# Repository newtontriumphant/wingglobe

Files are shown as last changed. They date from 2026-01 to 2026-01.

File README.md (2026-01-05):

# WingGlobe

Quick Link Tree:

* [I. Introduction!](#i-introduction)
* [II. About This Project - Why I Chose To Make It!](#ii-about-this-project---why-i-chose-to-make-it)
* [III. About This Project - What Is It?!](#iii-about-this-project---what-is-it)
* [IV. Project Images And Technical Documentation!](#iv-project-images-and-technical-documentation)
* [V. Notes For Reviewers!](#v-notes-for-reviewers)
* [VI. Final Remarks!](#vi-final-remarks)
  
## I. Introduction!

Heyo! Thanks for reviewing my project! I'm **zsharpminor** (a.k.a. funkeudo), co-creator of FiddleStein, and this is WingGlobe, which is a (TL;DR) fully autonomous Weather-Telling Snow Globe with a custom propulsion mechanism, PWM control, backlighting, E-INK display, support for my existing ecosystem of temperature sensors, and a changeable theme. This project is being created with the support of Hack Club Blueprint, and it is an entry for Blueprint's 7-day Christmas-Themed Project Competition. I am aiming for this to be a **Tier 3** project (see section at the very end of this README for justification).



(Disclaimer: the above image is a **render**, this project is not actually built yet; CAD screenshots can be found in section IV).

**IMPORTANT REVIEWER'S NOTE:** there is a section at the **end** of this README.md file, please read through it before returning this project if possible :)

My BOM.csv is in the parent directory, additionally a link to my online BOM is https://docs.google.com/spreadsheets/d/1PTxZxDy7cq01-oPVpPEEbVuQKtVb_WSBa-1fNMrsmt8/. Thanks! :3

Before I get into why I made this project, I would like to extend a huge thanks to can can't aka kleigh (my hero), as well as sam, alex, zach, renran, deven, paolo, john cohn, olive, my teammates Max & Sidd, tanuki, nathan, everyone from AMD, and every single other equally important person that made Blueprint & Prototype happen - I literally found out about Blueprint (and Hack Club itself!) only a month and a week ago, finished a few projects and became a reviewer one week later, had the most fun I've _ever_ had at Prototype, as well as inspired myself to get back into hardware, and re-dedicate my life to electronics. I really appreciate everything each and every one of you has done, and, without further ado, here's why WingGlobe exists.

## II. About This Project - Why I Chose To Make It!

You're probably looking at this and asking me "why the hell would you make a smart snow globe?!" The answer is a bit more complex than you think!

To start off with, I'm going to say quite bluntly that this project wouldn't exist without the Blueprint Christmas Competition. Even though I've worked with hardware for years, got HM with a self playing violin, and have been a Blueprint reviewer for over a month, I **don't actually own a 3D printer** (I've been using my local library's for all of my past projects so far)! I was planning on buying one a few weeks ago, then I set myself the challenge of getting one through Blueprint by reviewing a lot and getting tickets - but my current pace is rather lackluster. In addition, I needed ideas for projects to build - Blueprint is awesome because you can ship literally anything you can imagine, as long as it's under a certain dollar amount; but I was facing a bit of a creative block until this competition came about! My first project idea was to make a laser projecting 2026 New Year's countdown - but then I remembered that New Years would be over by the time this project would be built! My goal with WingGlobe was to make a project that, while Christmas-themed, **doesn't rely on Christmas to exist** and can be used **at any time of the year**! (Christmas in July, anyone?)

Additionally, I've made an ecosystem of projects (including one that I made through Blueprint - my SmartBell!) that feature temperature and humidity sensors. I wanted them to seamlessly work together wirelessly somehow, and needed a way to make that possible. That is also the main reason I chose the ESP32-S3 for this project, besides the fact that I already owned one, that it would cut PCBA cost in half, and that it would require one less parcel to be shipped.

Finally, I've been interested in weather and meteorology in general for a few years now, and I always wanted a weather station that relied on multiple sources of data that I myself provide, in addition to the commercial weather reports available.

The Snow Globe that builds this project's core features an empty space for _any_ 3d model or figurine (assuming it's heavy enough to withstand the fan blowing snow around it!) - and I've chosen a Christmas-themed one for my first few months with WingGlobe to fit the competition's theme.

Finally, if you're wondering why it's called WingGlobe, it's a reference to aviation, where meteorology is key (bad name, I know, but it stuck!)

I wanted WingGlobe to fit these criteria:

* It **must** be overwhelmingly Christmas-themed.
* It **must** have a decent amount of hardware complexity.
* It **must** be usable outside of just Christmas season.
* It **must** predominantly integrate CAD and software instead of being _just_ hardware.
* It **must** be actually useful in everyday life.
* The PCB **must** be under 100x100mm, eligible for GSDL, and Economic PCBA.
* All parts of the project **must** be printable on the Bambu A1 Mini with minimal supports and t*nkering.

I think I did a pretty good job fitting these criteria, if I do say so myself. Anyways, enough yapping, here's what the project actually _does_:

## III. About This Project - What Is It?!

WingGlobe is basically a glorified weather report station powered by a SEEED Studios XIAO ESP-32-S3 (that I already own - more on that in Section V) that runs 16 addressable SK6812-MINI LEDs, as well as an onboard temp/humi/pressure sensor and a MOSFET powering a 4010 fan with PWM control. When the weather shifts, the snow globe is updated to match - calm weather is a white / light-blue gradient and no fan power, sunny weather is a yellow / light red gradient, sunrise and sunset are adapted to red / orange gradients, and during the night, the snow globe will be engulfed in a replica of the aurora borealis (clear sky) or simply white / dark blue (cloudy sky). The real fun begins when it rains! When the winds start, the 4010 fan's PWM controller starts to rev it up - the more dangerous the wind, the more the little snow in the globe will swirl around! I am planning to use lightweight cotton / styrofoam blend beads to imitate snow (my original idea of 3D printing them sadly failed), as well as a custom mesh that stops them from breaking the fan or going out of the top of the globe. WingGlobe's E-Ink can be customized with a touch pad on WingGlobe's PCB to show varying levels of information from varying sensors. Additionally, the fan and LEDs can be turned off with a switch on WingGlobe's side when not needed (i.e. overnight).

WingGlobe seamlessly integrates with my SmartBell, moonboard, ADS-B stations, and BarnSense projects to provide up to three different simultaneous readings of temperature, humidity, and pressure. WingGlobe also has a built-in sensor for indoor temperature and humidity (should be quite useful next to my soon-to-be 3D Printer!) For now, WingGlobe relies on commercially available data for wind readings, but I hope to create another project soon so that everything can be run off the grid and without requiring any API.

WingGlobe's ESP32-S3 connects via ESP-NOW and WiFi to fetch data from my close and far stations, respectively. You're halfway there, have a cookie! 🍪

## IV. Project Images And Technical Documentation!

### SCHEMATIC:

Screenshot 2026-01-01 at 3 03 01 PM

### PCB:

Screenshot 2026-01-01 at 3 03 26 PM

Screenshot 2026-01-01 at 3 04 12 PM

Screenshot 2026-01-01 at 3 04 40 PM

### CAD:

Screenshot 2026-01-01 at 3 05 12 PM

(base, with cutouts for PCB, fan, and globe)

Screenshot 2026-01-01 at 3 05 39 PM

(top, made to be glued onto base)

### CAD WITH PCB:

Screenshot 2026-01-01 at 3 06 51 PM

(top view)

Screenshot 2026-01-01 at 3 07 16 PM

(side view)

Screenshot 2026-01-01 at 3 07 37 PM

(bottom view)

Screenshot 2026-01-01 at 3 08 41 PM

(top - birds-eye view without lid)

### ASSEMBLED PRODUCT:

Screenshot 2026-01-01 at 3 09 26 PM

(Front - Angle One)

Screenshot 2026-01-01 at 3 09 43 PM

(Front - Angle Two)

Screenshot 2026-01-01 at 3 10 05 PM

(Top)

Screenshot 2026-01-01 at 3 10 19 PM

(Side)

Screenshot 2026-01-01 at 3 10 37 PM

(Bottom)

### CARTS:

Screenshot 2026-01-04 at 6 10 24 PM

(AliExpress Checkout)

Screenshot 2026-01-01 at 3 34 09 PM

(JLCPCB PCB Options)

Screenshot 2026-01-01 at 3 33 00 PM

(JLCPCB PCBA 1)

Screenshot 2026-01-01 at 3 33 20 PM

(JLCPCB PCBA 2)

Screenshot 2026-01-01 at 3 33 39 PM

(JLCPCB PCBA 3)

Screenshot 2026-01-01 at 3 34 48 PM

(JLCPCB Pre-Discounts)

Screenshot 2026-01-04 at 6 09 27 PM

(JLCPCB Final Checkout As Shown On BOM)

**NOTE**: My name was redacted using the Inspect Element tool as this repository is publically visible. If an unredacted screenshot is required, please DM me or return my project.

### I will self-fund the E-INK display due to the project tier being bumped down to T4.

### RENDER:



(My friend with Blender skills did this and it turned out amazing, so I'm making this my cover image!)

## V. Notes For Reviewers!

### Usage Of Pre-Built Devboard:

I chose to use the XIAO ESP32-S3 over making a custom ESP32 or RP2040 devboard base for three reasons:

1. I already own quite a few ESP32-S3s, making an ESP32 from scratch would more than **double** the PCBA cost at JLC, and make my order **ineligible** for GSDL shipping, which would push my budget to Tier 2.
2. I've already made a devboard, I know the hassles that are involved in wiring and routing, and I did not want to miss a single decoupling capacitor and risk my board being browned out.
3. I wanted to spend more time polishing software and CAD, and using a pre-built devboard gave me that opportunity.

Again, if this cannot be approved for Tier 3 due to a lack of complexity, I understand, and will remove parts to bring the budget down to a Tier 4.

### Why Are You Requesting Six Snow Globes?

Because it's the cheapest option available for a half-decent snowglobe on AliExpress. The next-cheapest was $7 for two, and I preferred to get six for $6.88.

All of my costs are optimized as **much as possible**, I'm using AliExpress for my items, and I've done my best to keep it in budget.

### Why Are You Requesting $10 More Than You Need For JLCPCB?

JLCPCB has a $10 coupon for PCBA (scroll up to the images section for proof). Said coupon expires in 2 days, and, knowing HCB, it will take more than 2 days to process this grant. If another coupon appears, I will return the difference immediately.

### "ThIs ReADmE iS AI gEnEraTEd!"

No, no it's not. I know how to use markdown, and I'll even occasionally use an em-dash—like so. That doesn't necessarily mean my README is automatically AI. Zero AI was used in the making of this project, and writing this text-heavy README alone took me two hours. If you need proof, I can provide a screen recording!

That's all, thanks! :D

## VI. Final Remarks!

Please ping or DM me on Slack (@zsharpminor) if you have any questions regarding my project.

Thank you so much for taking your precious time to read all the way through this extremely long README (I wanted to be well documented, okay?!)

You get a massive slice of vanilla cheesecake! :D 🍰

P.S. Happy New Year!!! I worked on this project literally as the clock struck 12 - I have a journal entry to prove it :)

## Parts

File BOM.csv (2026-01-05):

WingGlobe BOM
AliExpress Item | Link | Description | Price | Quantity | Running Total
1 | https://www.aliexpress.us/item/3256805177029030.html | (WHITE, 2-3.5mm 13g); used as snow | $2.08 | 1x 13g | $2.08
2 | https://www.aliexpress.us/item/3256806072050927.html | (SS12D06G5 10PCS); used for on/off | $1.76 | 1x 10 | $3.84
4 | https://www.aliexpress.us/item/3256807169365804.html | (6PCS with AL lid); snow globe housing | $6.88 | 1x 6 | $10.72
5 | https://www.aliexpress.us/item/3256806120222119.html | (5V, 4010); fan to power snow | $2.06 | 1x 1 | $12.69
AliExpress Total: | $12.69
JLCPCB Item
PCB | N/A | What makes WingGlobe work! | $2.00 | 1x 5 | $2.00
PCBA | N/A | Pay those poor Chinese laborers! | $25.63 | 1x 2 | $27.63
Shipping | N/A | This is GSDL - check screenshot for proof. | $14.63 | 1x 1 | $42.26
Taxes | N/A | I wish I was tax-exempt... | $1.79 | 1x 1 | $44.05
Payment Fee | N/A | What is this for, anyways?! | $0.50 | 1x 1 | $44.55
Discount | N/A | Hooray! | -$9.00 | 1x 1 | $35.55
JLCPCB Total: | $35.55
GRAND TOTAL: | $48.24
ROUNDED TOTAL: | $50
Notes: | My detailed JLCPCB BOM for PCBA and proof of GSDL are in cart screenshots.
 | If required, the detailed PCBA breakdown can be individually listed. Please DM me.

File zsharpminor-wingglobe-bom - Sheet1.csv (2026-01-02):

WingGlobe BOM
AliExpress Item | Link | Description | Price | Quantity | Running Total
1 | https://www.aliexpress.us/item/3256805177029030.html | (WHITE, 2-3.5mm 13g); used as snow | $2.08 | 1x 13g | $2.08
2 | https://www.aliexpress.us/item/3256806072050927.html | (SS12D06G5 10PCS); used for on/off | $1.76 | 1x 10 | $3.84
3 | https://www.aliexpress.us/item/3256805040417601.html | (SINK0290B2-BRW); used as display | $9.99 | 1x 1 | $13.83
4 | https://www.aliexpress.us/item/3256807169365804.html | (6PCS with AL lid); snow globe housing | $6.88 | 1x 6 | $20.71
5 | https://www.aliexpress.us/item/3256806120222119.html | (5V, 4010); fan to power snow | $2.06 | 1x 1 | $22.77
Shipping |  | Cheapest Possible | $8.97 | 1x 1 | $31.74
Taxes |  | I don't do tax evasion ;w; | $1.86 | 1x 1 | $33.60
Estimated Coupon |  | I hope this'll still be there! | -$0.20 | 1x 1 | $33.40
AliExpress Total: | $33.40
JLCPCB Item
PCB | N/A | What makes WingGlobe work! | $2.00 | 1x 5 | $2.00
PCBA | N/A | Pay those poor Chinese laborers! | $25.63 | 1x 2 | $27.63
Shipping | N/A | This is GSDL - check screenshot for proof. | $14.63 | 1x 1 | $42.26
Taxes | N/A | I wish I was tax-exempt... | $2.62 | 1x 1 | $44.88
Payment Fee | N/A | What is this for, anyways?! | $0.50 | 1x 1 | $45.38
JLCPCB Total: | $45.38
GRAND TOTAL: | $78.78
ROUNDED TOTAL: | $80
Notes: | My detailed JLCPCB BOM for PCBA and proof of GSDL are in cart screenshots.
 | If required, the detailed PCBA breakdown can be individually listed. Please DM me.
 | JLCPCB has a $10 coupon BUT it expires on January 3rd, which is why it's not
 | accounted for in this BOM. If another coupon becomes available, I will return the
 | extra $10.

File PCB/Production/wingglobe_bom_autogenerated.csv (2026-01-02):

Designator | Footprint | Quantity | Value | LCSC Part #
C1 | 0402 | 1 | 10 uF
C2 | 0402 | 1 | 0.1uF
D1, D10, D11, D12, D13, D14, D15, D16, D2, D3, D4, D5, D6, D7, D8, D9 | LED_SK6812MINI_PLCC4_3.5x3.5mm_P1.75mm | 16 | SK6812MINI
J1 | JST_XH_B2B-XH-A_1x02_P2.50mm_Vertical | 1 | Conn_01x02
J2 | PinHeader_1x08_P2.54mm_Vertical | 1 | Conn_01x08
Q1 | SOT-23 | 1 | AO3400A
R1 | 0402 | 1 | 330
R2 | 0402 | 1 | 10k
R3, R4 | 0402 | 2 | 4.7k
SW1 | SW_Slide_SPDT_Angled_CK_OS102011MA1Q | 1 | SW_SPDT
TP1 | TestPoint_Pad_D4.0mm | 1 | TOUCH
U1 | XIAO-ESP32S3-DIP | 1 | XIAO-ESP32-S3-DIP
U2 | Texas_PWSON-N6 | 1 | HDC1080

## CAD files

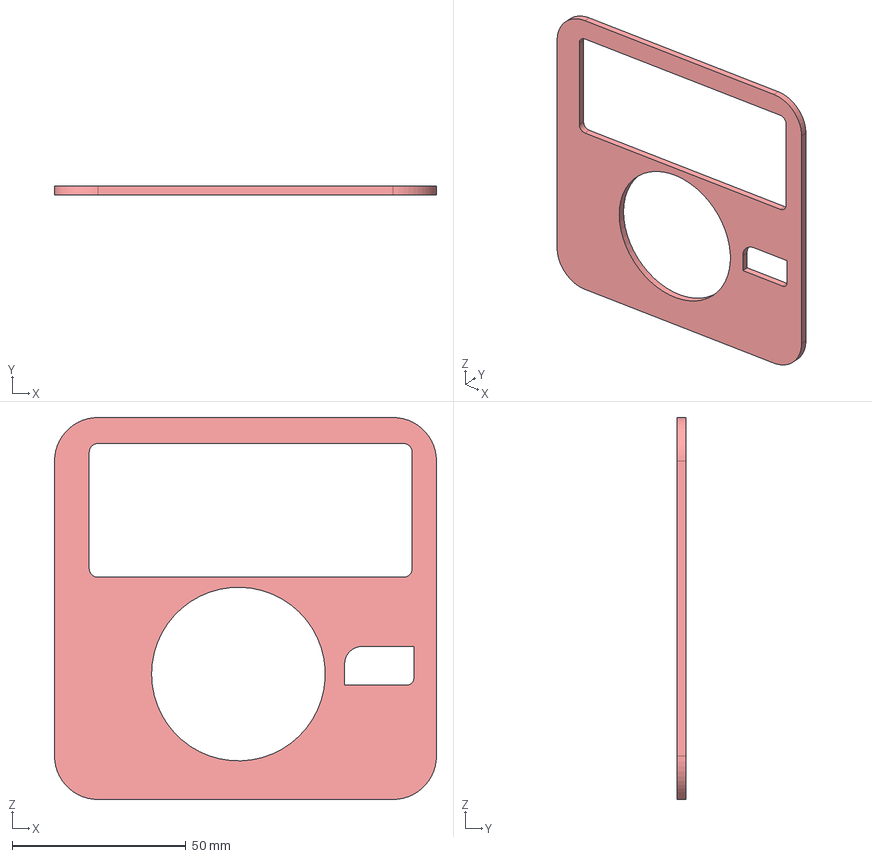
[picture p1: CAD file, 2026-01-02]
CAD/Housing/wingglobe_top.step
110.0 x 2.50 x 110.0 mm

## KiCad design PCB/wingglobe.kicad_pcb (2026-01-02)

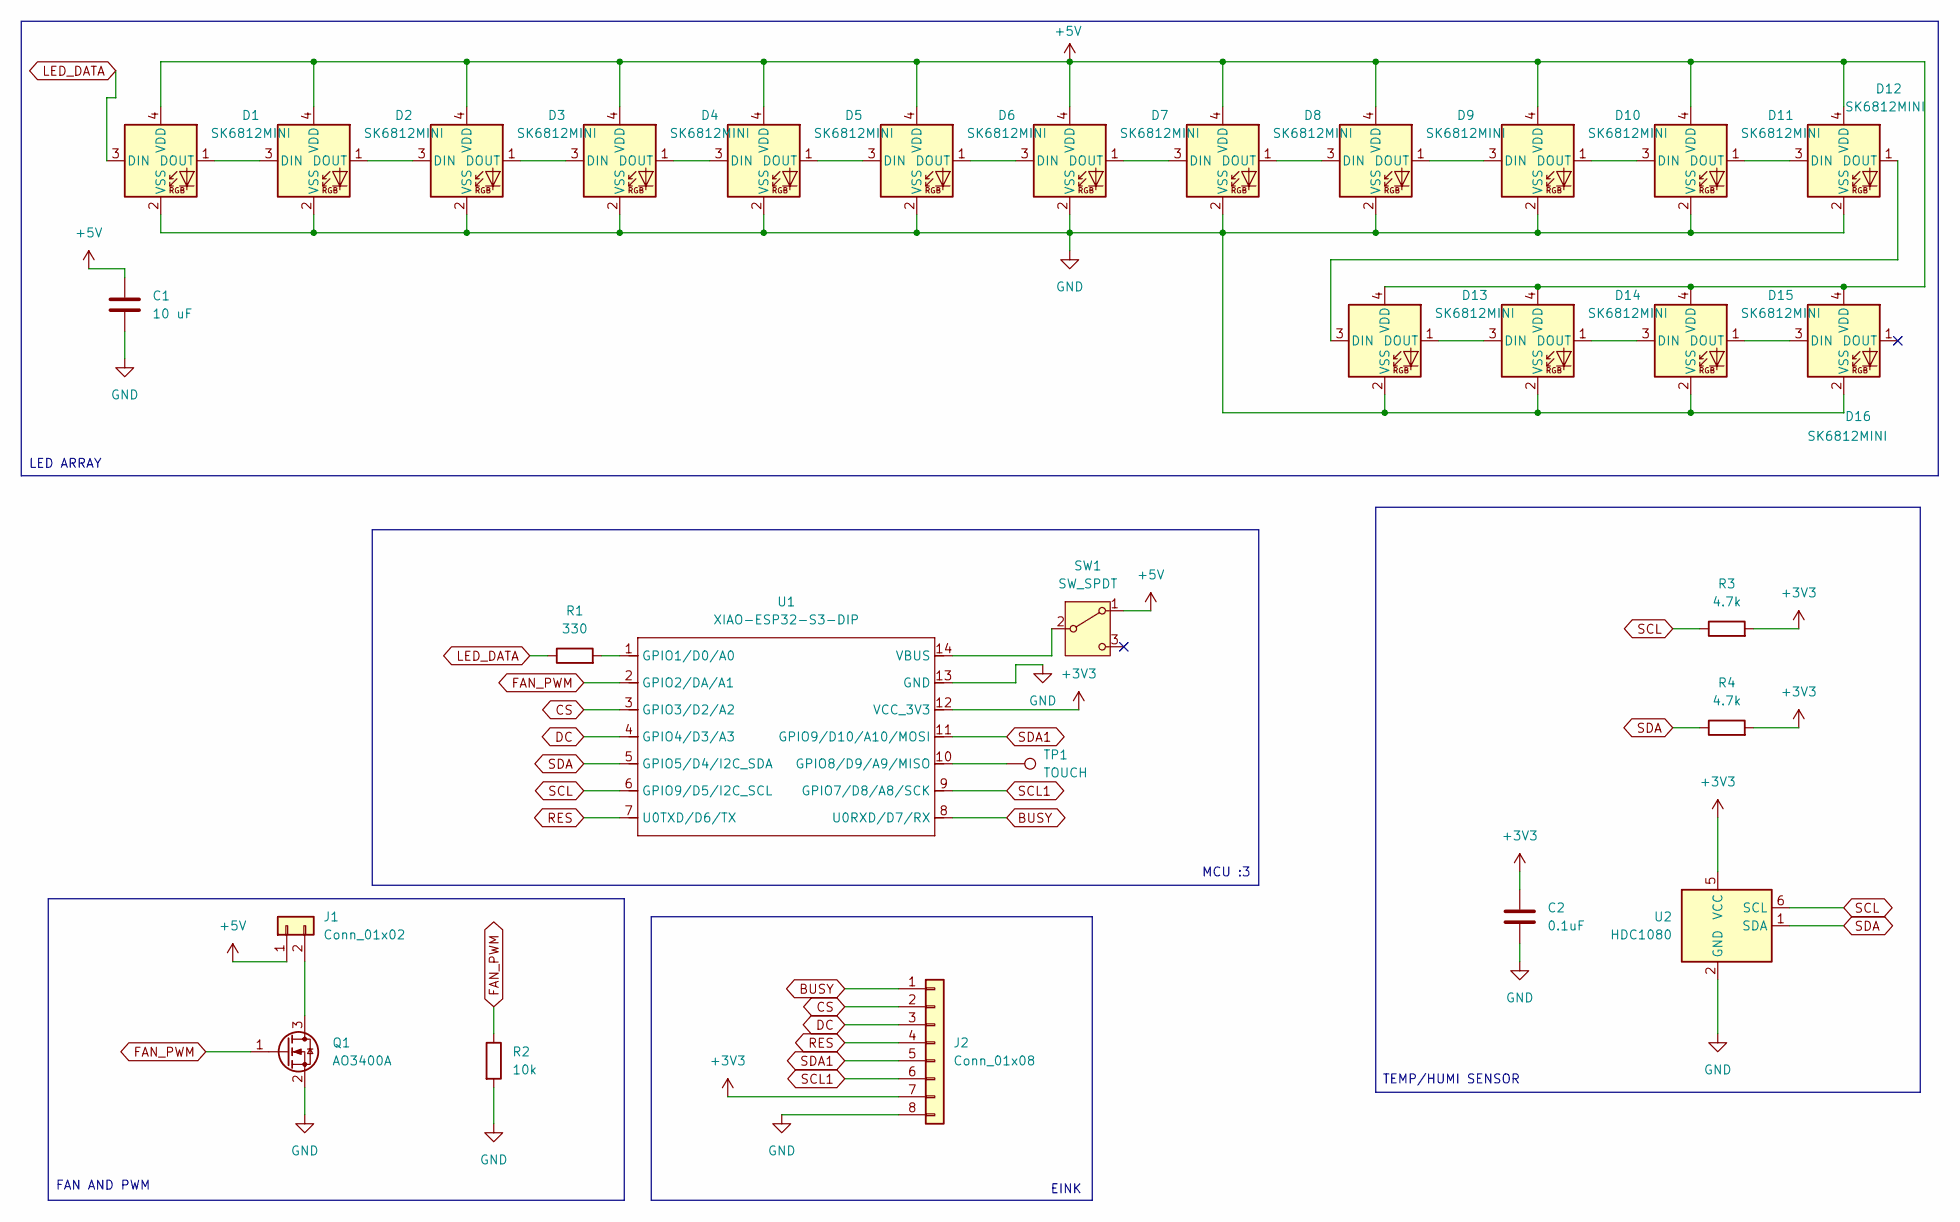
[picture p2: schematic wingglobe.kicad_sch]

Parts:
C1: 10 uF; C_0402_1005Metric
C2: 0.1uF; C_0402_1005Metric
D1, D2, D3, D4, D5, D6, D7, D8, D9, D10, D11, D12, D13, D14, D15, D16: SK6812MINI; LED_SK6812MINI_PLCC4_3.5x3.5mm_P1.75mm
J1: Conn_01x02; JST_XH_B2B-XH-A_1x02_P2.50mm_Vertical
J2: Conn_01x08; PinHeader_1x08_P2.54mm_Vertical
Q1: AO3400A; SOT-23
R1: 330; R_0402_1005Metric
R2: 10k; R_0402_1005Metric
R3, R4: 4.7k; R_0402_1005Metric
SW1: SW_SPDT; SW_Slide_SPDT_Angled_CK_OS102011MA1Q
TP1: TOUCH; TestPoint_Pad_D4.0mm
U1: XIAO-ESP32-S3-DIP; XIAO-ESP32S3-DIP
U2: HDC1080; Texas_PWSON-N6

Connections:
+3V3: C2.1, J2.7, R3.2, R4.2, U1.12 (VCC_3V3), U2.5 (VCC)
+5V: C1.1, D1.4 (VDD), D2.4 (VDD), D3.4 (VDD), D4.4 (VDD), D5.4 (VDD), D6.4 (VDD), D7.4 (VDD), D8.4 (VDD), D9.4 (VDD), D10.4 (VDD), D11.4 (VDD), D12.4 (VDD), D13.4 (VDD), D14.4 (VDD), D15.4 (VDD), D16.4 (VDD), J1.1, SW1.1 (A)
BUSY: J2.1, U1.8 (U0RXD/D7/RX)
CS: J2.2, U1.3 (GPIO3/D2/A2)
DC: J2.3, U1.4 (GPIO4/D3/A3)
FAN_PWM: Q1.1 (G), R2.1, U1.2 (GPIO2/DA/A1)
GND: C1.2, C2.2, D1.2 (VSS), D2.2 (VSS), D3.2 (VSS), D4.2 (VSS), D5.2 (VSS), D6.2 (VSS), D7.2 (VSS), D8.2 (VSS), D9.2 (VSS), D10.2 (VSS), D11.2 (VSS), D12.2 (VSS), D13.2 (VSS), D14.2 (VSS), D15.2 (VSS), D16.2 (VSS), J2.8, Q1.2 (S), R2.2, U1.13 (GND), U2.2 (GND)
LED_DATA: D1.3 (DIN), R1.1
unnamed: D1.1 (DOUT), D2.3 (DIN)
unnamed: D2.1 (DOUT), D3.3 (DIN)
unnamed: D3.1 (DOUT), D4.3 (DIN)
unnamed: D4.1 (DOUT), D5.3 (DIN)
unnamed: D5.1 (DOUT), D6.3 (DIN)
unnamed: D6.1 (DOUT), D7.3 (DIN)
unnamed: D7.1 (DOUT), D8.3 (DIN)
unnamed: D8.1 (DOUT), D9.3 (DIN)
unnamed: D9.1 (DOUT), D10.3 (DIN)
unnamed: D10.1 (DOUT), D11.3 (DIN)
unnamed: D11.1 (DOUT), D12.3 (DIN)
unnamed: D12.1 (DOUT), D13.3 (DIN)
unnamed: D13.1 (DOUT), D14.3 (DIN)
unnamed: D14.1 (DOUT), D15.3 (DIN)
unnamed: D15.1 (DOUT), D16.3 (DIN)
unnamed: J1.2, Q1.3 (D)
unnamed: SW1.2 (B), U1.14 (VBUS)
unnamed: R1.2, U1.1 (GPIO1/D0/A0)
unnamed: TP1.1, U1.10 (GPIO8/D9/A9/MISO)
RES: J2.4, U1.7 (U0TXD/D6/TX)
SCL: R3.1, U1.6 (GPIO9/D5/I2C_SCL), U2.6 (SCL)
SCL1: J2.6, U1.9 (GPIO7/D8/A8/SCK)
SDA: R4.1, U1.5 (GPIO5/D4/I2C_SDA), U2.1 (SDA)
SDA1: J2.5, U1.11 (GPIO9/D10/A10/MOSI)

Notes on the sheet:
TEMP/HUMI SENSOR
FAN AND PWM
EINK
MCU :3
LED ARRAY

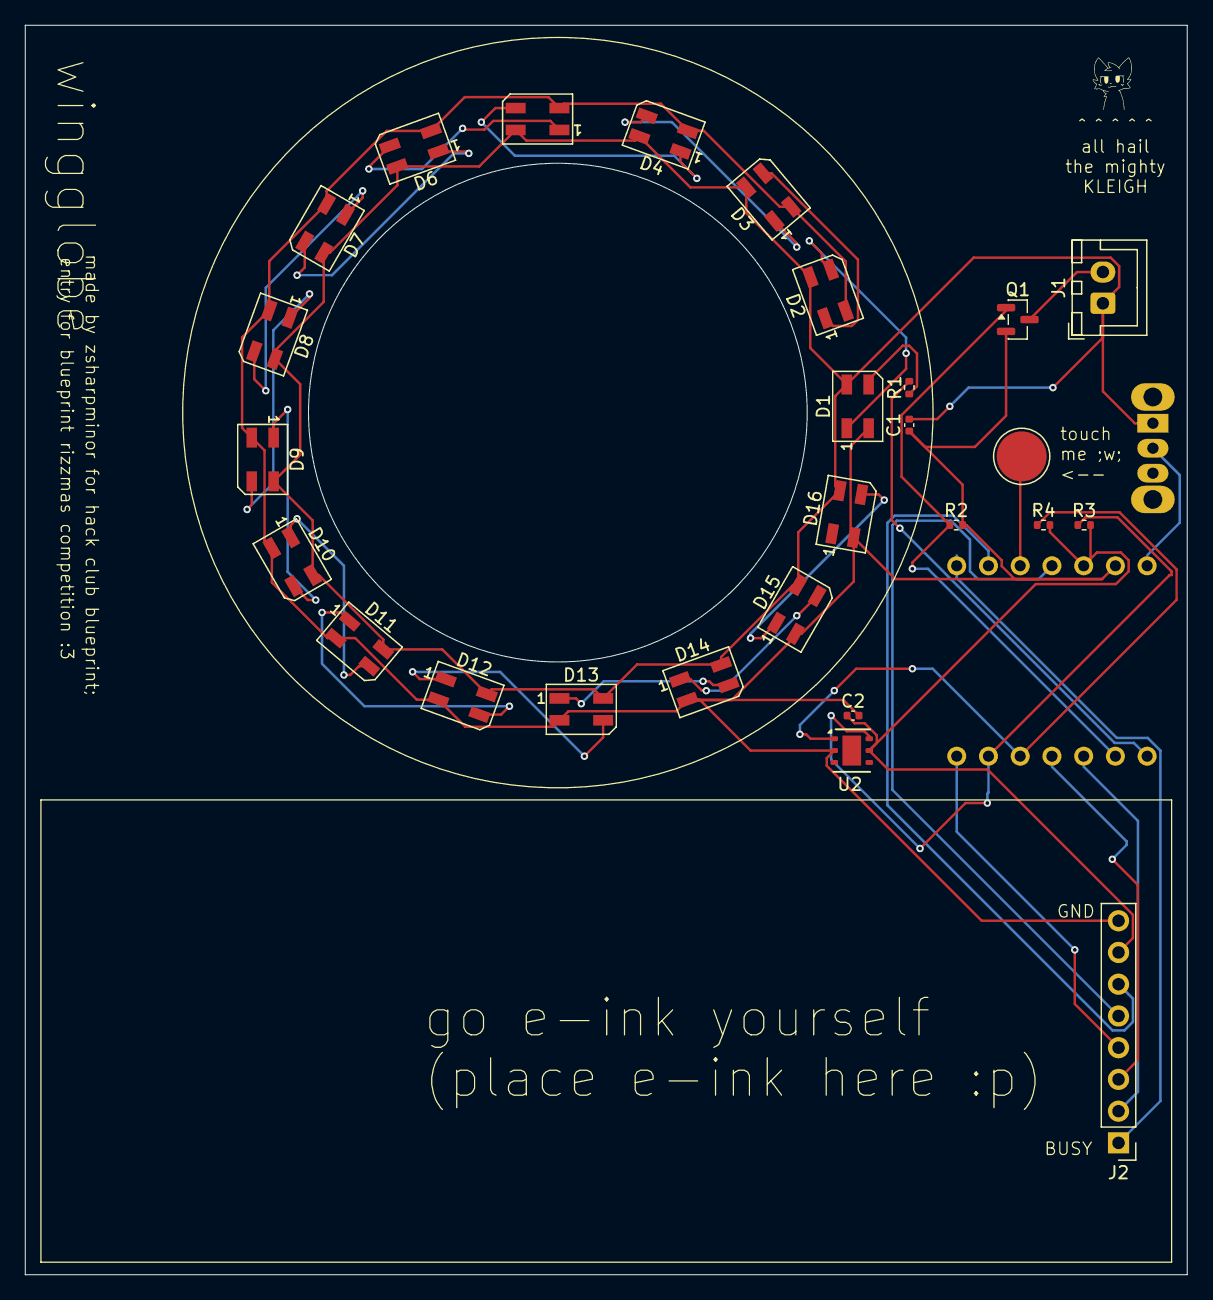
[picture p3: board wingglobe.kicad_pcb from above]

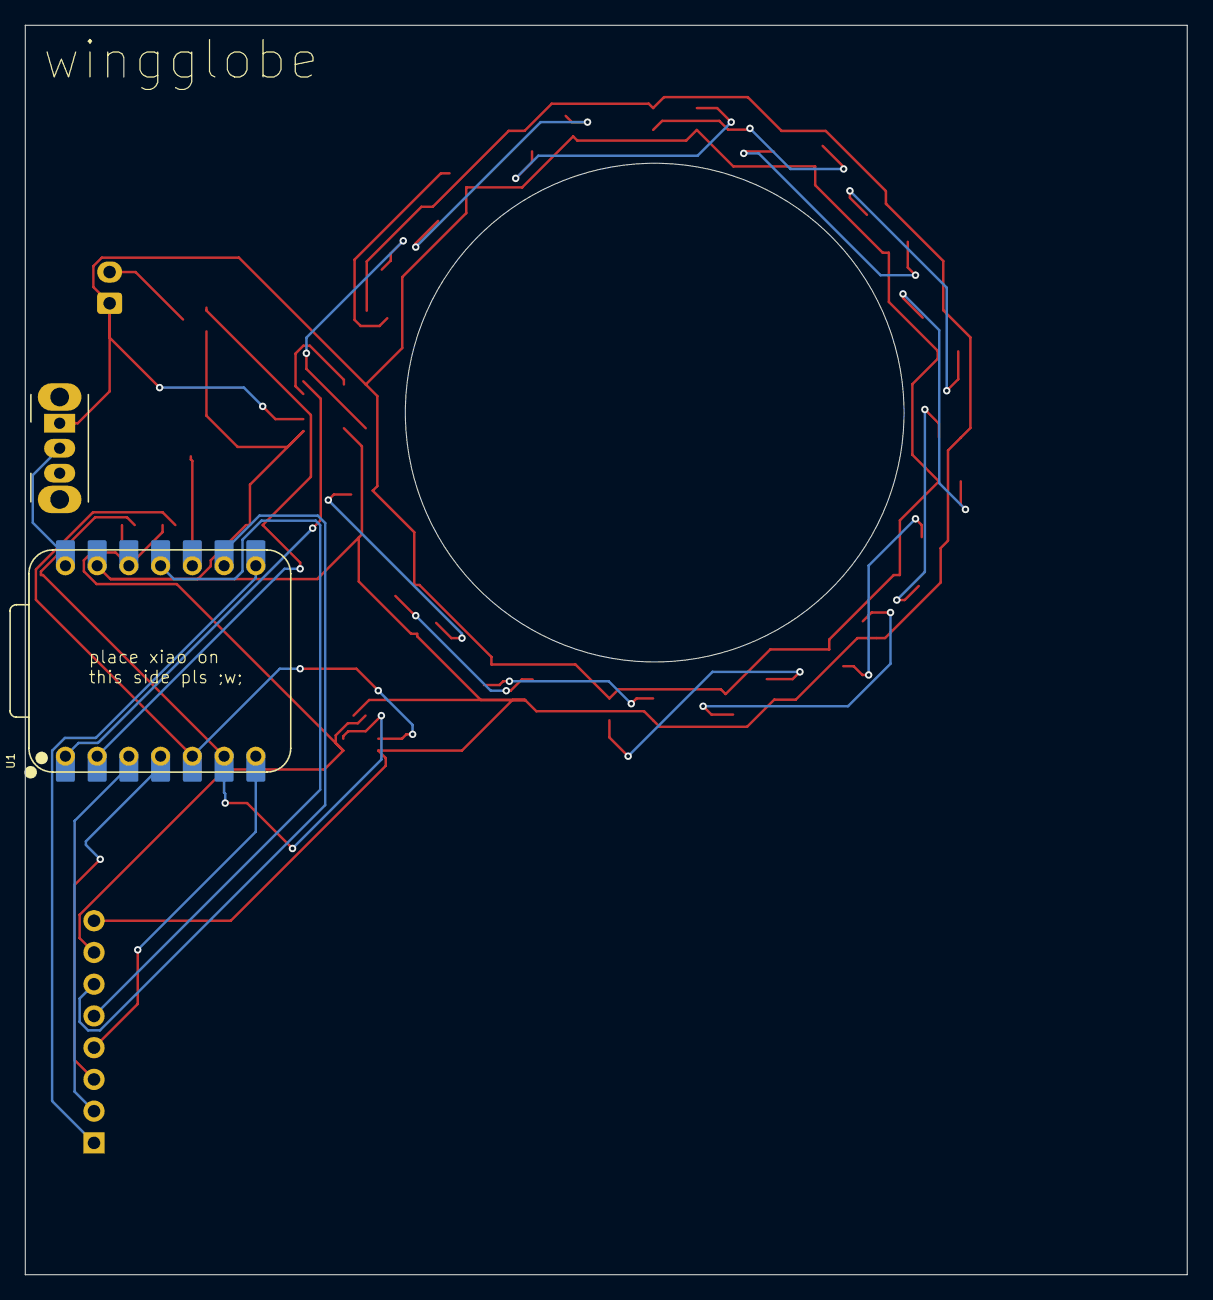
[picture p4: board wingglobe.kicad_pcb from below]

Board: 2 copper layers, 93.0 x 100.0 mm, 29 parts (2 on the bottom side), 32 nets.

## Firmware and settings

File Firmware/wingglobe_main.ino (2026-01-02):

/*
 * WingGlobe by zsharpminor :3
 * This code is NOT final and will be adjusted once parts in hand!!
 * Only uses the inbuilt sensor for now as I'm tired, I'll add the switching mechanic later.
 */

#include <WiFi.h>
#include <HTTPClient.h>
#include <Arduino_JSON.h>
#include <Adafruit_NeoPixel.h>
#include <Wire.h>
#include "ClosedCube_HDC1080.h"
#include <GxEPD2_3C.h>
#include <SPI.h>

const char* WIFI_SSID     = "redacted_for_privacy";
const char* WIFI_PASS     = "what_ru_looking_for_weatherboy";
String OWM_API_KEY        = "i_said_redacted";
String CITY               = "Mill Valley";
String COUNTRY            = "US";

#define PIN_FAN_MOSFET    2
#define PIN_LEDS          1
#define NUM_LEDS          16
#define PIN_I2C_SDA       5
#define PIN_I2C_SCL       6

#define EINK_CS           3
#define EINK_DC           4
#define EINK_RST          43
#define EINK_BUSY         44
#define EINK_SCK          7
#define EINK_MOSI         9

GxEPD2_3C<GxEPD2_290_Z13c, GxEPD2_290_Z13c::HEIGHT> display(GxEPD2_290_Z13c(EINK_CS, EINK_DC, EINK_RST, EINK_BUSY));

Adafruit_NeoPixel strip(NUM_LEDS, PIN_LEDS, NEO_GRB + NEO_KHZ800);
ClosedCube_HDC1080 hdc1080;

unsigned long lastTime = 0;
unsigned long timerDelay = 600000;

void setup() {
  Serial.begin(115200);

  pinMode(PIN_FAN_MOSFET, OUTPUT);
  ledcAttach(PIN_FAN_MOSFET, 25000, 8);

  strip.begin();
  strip.show();

  Wire.begin(PIN_I2C_SDA, PIN_I2C_SCL);
  hdc1080.begin(0x40);

  SPI.begin(EINK_SCK, -1, EINK_MOSI, EINK_CS);
  display.init(0);
  display.setRotation(3);

  WiFi.begin(WIFI_SSID, WIFI_PASS);
  while(WiFi.status() != WL_CONNECTED) {
    delay(500);
  }

  updateWeather();
}

void loop() {
  if ((millis() - lastTime) > timerDelay) {
    updateWeather();
    lastTime = millis();
  }
}

void updateWeather() {
  if(WiFi.status() != WL_CONNECTED) return;

  String url = "http://api.openweathermap.org/data/2.5/weather?q=" + CITY + "," + COUNTRY + "&APPID=" + OWM_API_KEY + "&units=metric";
  
  WiFiClient client;
  HTTPClient http;
  http.begin(client, url);
  int httpCode = http.GET();
  
  if (httpCode > 0) {
    String payload = http.getString();
    JSONVar data = JSON.parse(payload);

    if (JSON.typeof(data) != "undefined") {
      double temp = (double)data["main"]["temp"];
      int humidity = (int)data["main"]["humidity"];
      double wind = (double)data["wind"]["speed"];
      int id = (int)data["weather"][0]["id"];
      String desc = (const char*)data["weather"][0]["description"];

      double localTemp = hdc1080.readTemperature();
      double localHum = hdc1080.readHumidity();

      setFan(wind);
      setLeds(id);
      drawDisplay(temp, humidity, wind, desc, localTemp, localHum);
    }
  }
  http.end();
}

void setFan(double speed) {
  int pwm = map((long)speed, 0, 15, 0, 255);
  pwm = constrain(pwm, 0, 255);
  ledcWrite(PIN_FAN_MOSFET, pwm);
}

void setLeds(int id) {
  uint32_t c1, c2;

  if (id >= 200 && id < 300) { 
    c1 = strip.Color(150, 150, 150); c2 = strip.Color(0, 0, 100);
  } else if (id >= 300 && id < 600) { 
    c1 = strip.Color(0, 0, 255); c2 = strip.Color(0, 0, 50);
  } else if (id >= 800 && id < 802) { 
    c1 = strip.Color(255, 255, 0); c2 = strip.Color(255, 100, 0);
  } else if (id >= 802) { 
    c1 = strip.Color(200, 200, 200); c2 = strip.Color(100, 100, 255);
  } else {
    c1 = strip.Color(50, 50, 50); c2 = strip.Color(0, 0, 0);
  }

  for(int i=0; i<NUM_LEDS; i++) {
    float r = (float)i / (NUM_LEDS - 1);
    uint8_t red = (uint8_t)(( (c1 >> 16) * (1-r)) + ((c2 >> 16) * r));
    uint8_t grn = (uint8_t)(( ((c1 >> 8) & 0xFF) * (1-r)) + ((c2 >> 8 & 0xFF) * r));
    uint8_t blu = (uint8_t)(( (c1 & 0xFF) * (1-r)) + ((c2 & 0xFF) * r));
    strip.setPixelColor(i, strip.Color(red, grn, blu));
  }
  strip.show();
}

void drawDisplay(double t, int h, double w, String d, double lt, double lh) {
  display.setFullWindow();
  display.firstPage();
  do {
    display.fillScreen(GxEPD_WHITE);
    
    display.setTextColor(GxEPD_BLACK);
    display.setTextSize(1);
    display.setCursor(0, 10);
    display.println("WEATHER STATION");
    
    display.setTextSize(2);
    display.setCursor(0, 30);
    display.print(t, 1); display.print("C "); display.print(h); display.println("%");
    
    display.setTextColor(GxEPD_RED);
    display.setTextSize(1);
    display.setCursor(0, 55);
    display.print("Wind: "); display.print(w); display.println(" m/s");
    display.println(d);

    display.setTextColor(GxEPD_BLACK);
    display.drawLine(0, 80, display.width(), 80, GxEPD_BLACK);

    display.setCursor(0, 90);
    display.println("INDOOR:");
    display.setTextSize(2);
    display.setCursor(0, 105);
    display.print(lt, 1); display.print("C "); display.print(lh, 0); display.println("%");

  } while (display.nextPage());
}

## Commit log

2026-01-02 Add BOM.csv
    [zsharpminor-wingglobe-bom - Sheet1.csv]
2026-01-02 Added Full Housing Files
2026-01-02 Added Top Housing Files
    [wingglobe_top.step]
2026-01-02 Added Bottom Housing Files
2026-01-02 Added Assembled Files
2026-01-02 Added All Final CAD Files
2026-01-02 Added All KiCad Files
    [wingglobe.kicad_pcb, wingglobe.kicad_sch]
2026-01-02 Added All Production Files And Gerbers
    [wingglobe_bom_autogenerated.csv, wingglobe_designators.csv, wingglobe_positions.csv]
2026-01-02 Added All Final PCB Files
2026-01-05 Fixed BOM.csv
    Updated BOM with new item prices and totals.
    [BOM.csv]
2026-01-05 Update BOM.csv with new formatting and data
    [BOM.csv]
